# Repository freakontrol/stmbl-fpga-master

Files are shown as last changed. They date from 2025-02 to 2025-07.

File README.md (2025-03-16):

DISCLAIMER
===

THE AUTHORS OF THIS SOFTWARE ACCEPT ABSOLUTELY NO LIABILITY FOR
ANY HARM OR LOSS RESULTING FROM ITS USE.  IT IS _EXTREMELY_ UNWISE
TO RELY ON SOFTWARE ALONE FOR SAFETY.  Any machinery capable of
harming persons must have provisions for completely removing power
from all motors, etc, before persons enter any danger area.  All
machinery must be designed to comply with local and national safety
codes, and the authors of this software can not, and do not, take
any responsibility for such compliance.

This firmware in the folder hostmot2-firmware originates from Mesa Electronics.
This repository  is released under the GPLv3.

STMBL FPGA Master
=====

This is a FPGA controller board specifically designed to be used as a master for up to 12 stmbl drives. It can be used for other applications.
The hardware has the same form factor as the [STMBL](https://github.com/freakontrol/stmbl) v5 drives.
The FPGA runs the hostmot2 firmware.

## Hardware overview
- 12 SSerial ports
- 2 SSerial/RS485 ports
- one 26 Pin parallel expansion port (17 IOs)
- one 24V Input
- one 24V Output
- Host connection via Ethernet or SPI (if used with a RPi 4 or 5)
- 24V Power Input (provides also power to the Raspberry Pi)

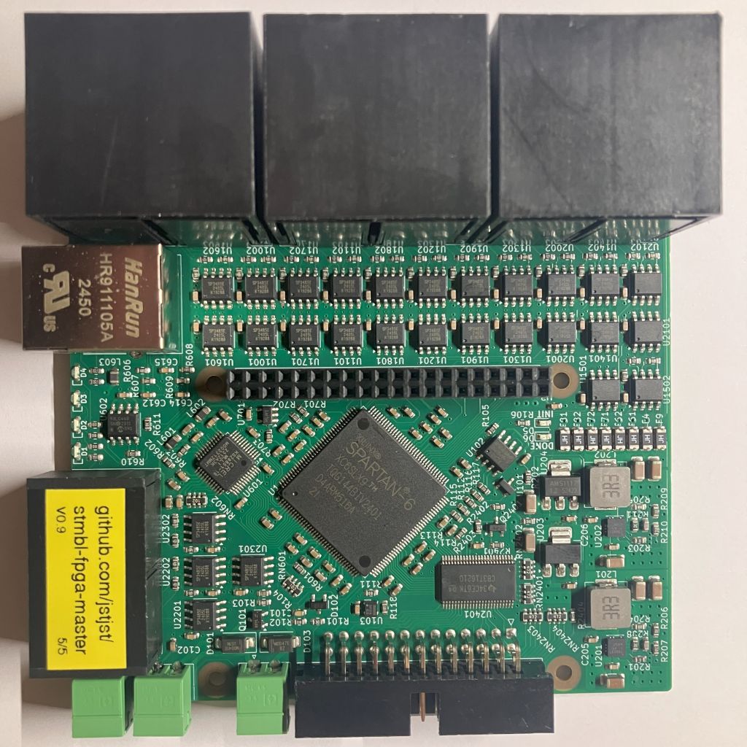
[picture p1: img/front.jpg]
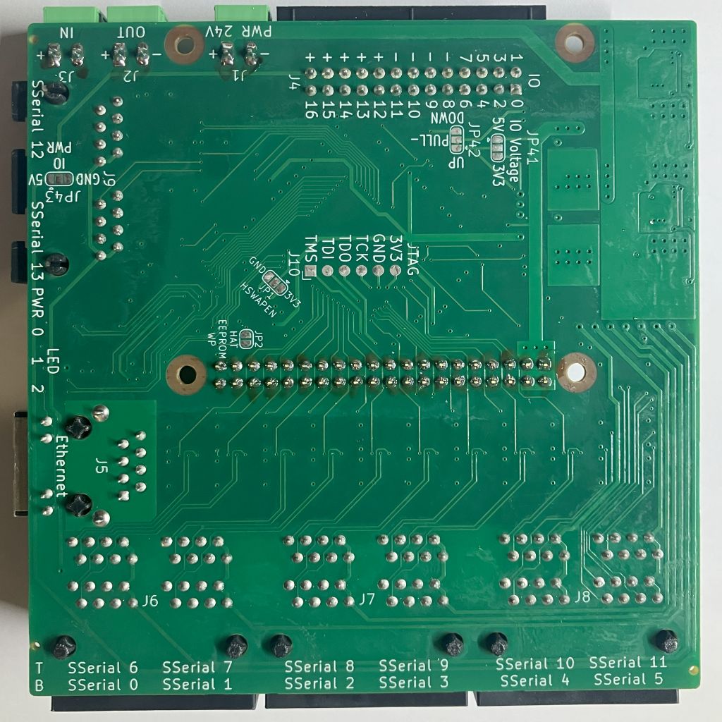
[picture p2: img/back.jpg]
  

## Known Bugs

**Please note that the hardware and firmware are in an early prototyping stage.**
Don't manufacture the version 0.9 because of the reversed SSerial pinouts

- affects hardware v0.9: Pinout of SSerial 0-5 and 12-13 is reversed (1-8, 2-7, ...), use a [Rollover cable](https://en.wikipedia.org/wiki/Rollover_cable)
- SSerial 13 ist not working, there seems to be a bug in the PIN file
- At the moment there is no option to enable power to the SSerial ports before loading the hm2 driver. So it is not possible to use SSerial devices that a powered form the SSerial connector. Can be fixed in firmware.

* * * 
If you have questions about this project contact me [here](https://matrix.to/#/@jst:freiburg.social).

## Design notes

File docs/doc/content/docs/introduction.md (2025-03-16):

---
title: "Introduction"
weight: 1
# bookFlatSection: true
bookToc: true
# bookHidden: false
# bookCollapseSection: true
# bookComments: true
# bookSearchExclude: false
---

# STMBL FPGA Master Introduction Guide

## Description

This is a FPGA controller board specifically designed to be used as a master for up to 12 stmbl drives. It can be used for other applications.
The hardware has the same form factor as the [STMBL](https://github.com/freakontrol/stmbl) v5 drives.
The FPGA runs the hostmot2 firmware.

## Anatomy of the STMBL FPGA Master

The STMBL FPGA Master uses a Spartan 6 and can be either connected via ethernet or SPI to a LinuxCNC host. The board is designed to carry a Raspberry Pi 4 or 5 with the SPI host interface connections.
The board also supplies power to the Raspberry Pi.

{{% hint danger %}}
 Don't connect a USB C power supply to the Raspberry Pi.
{{% /hint %}}

It is also possible to use the board without a Raspberry Pi and connect a host via ethernet.

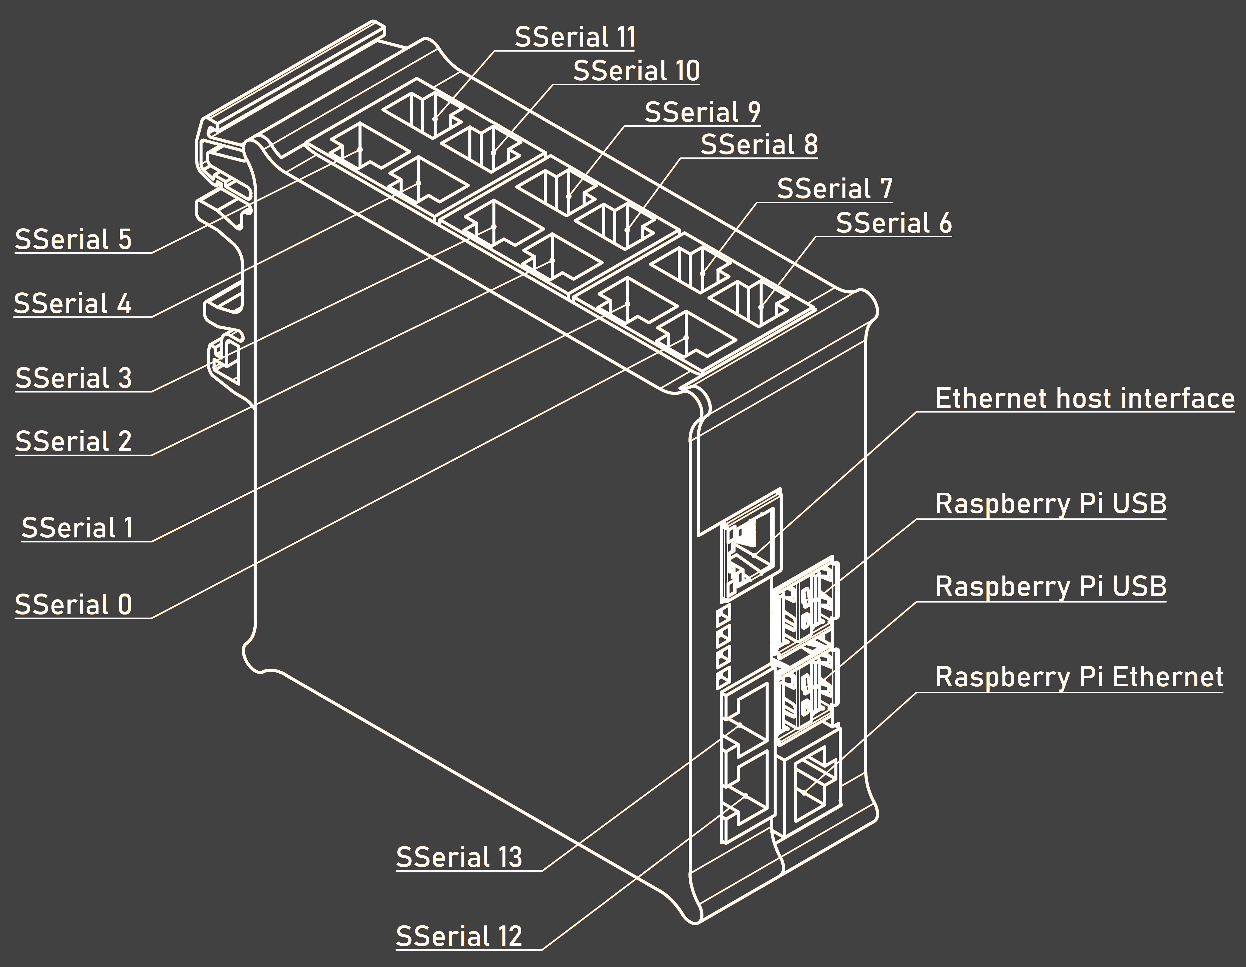
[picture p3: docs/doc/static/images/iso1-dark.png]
STMBL FPGA Master Anatomy


{{% hint danger %}}
 In Hardware v0.9, the Pinout of SSerial 0-5 and 12-13 is reversed (1-8, 2-7, ...), use a [Rollover cable](https://en.wikipedia.org/wiki/Rollover_cable).
{{% /hint %}}

Power to the board should be 24V. A green LED will light when power is supplied.
The board could draw up to 80W if it supplies the SSerial daughter boards and the Raspberry Pi (and USB devices).
For standalone usage the board draws about 2-3W.

{{% hint warning %}}
 A high power consumption is not tested yet, the DC-DC converters might need additional cooling.
{{% /hint %}}

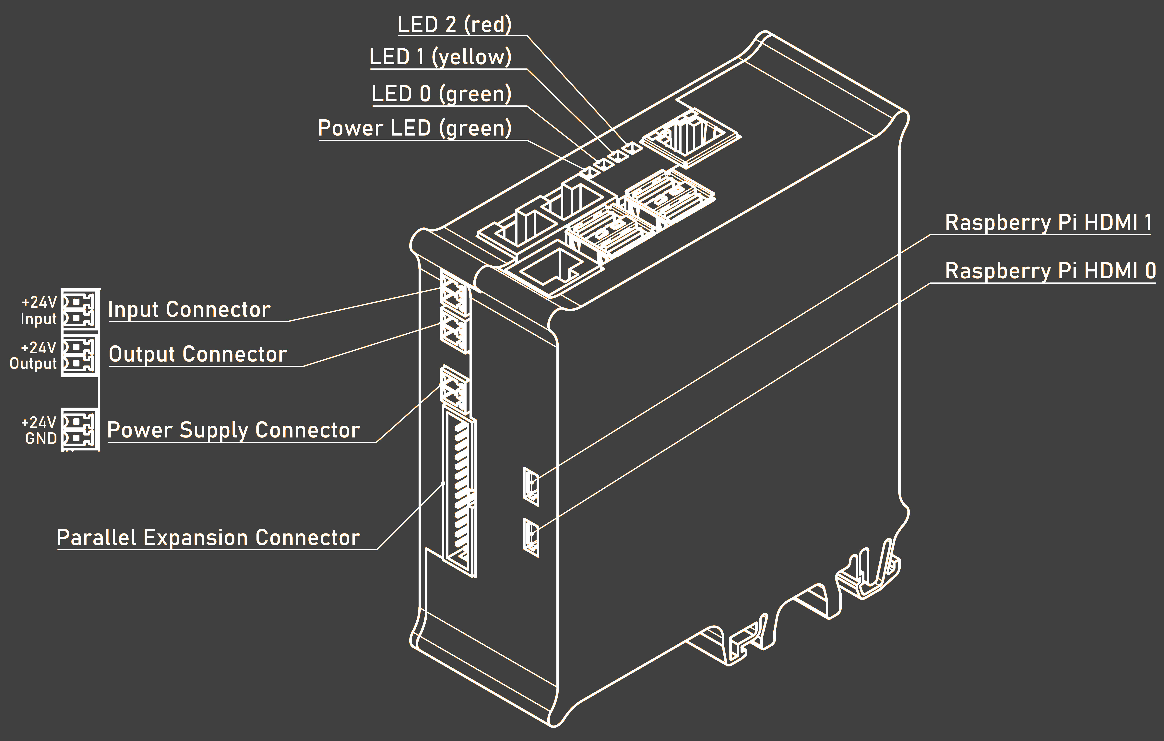
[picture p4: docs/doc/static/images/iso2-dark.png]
STMBL FPGA Master Connectors


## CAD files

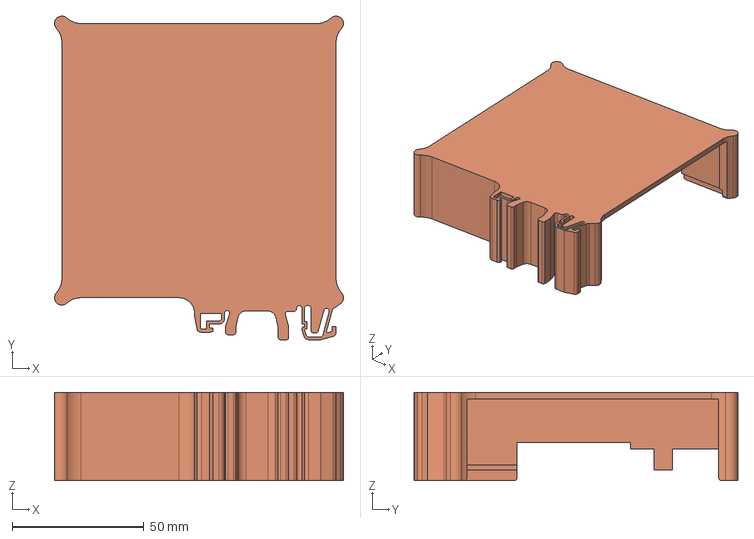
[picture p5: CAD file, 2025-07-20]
3dmodels/stmblv5_ss-kitcase.step
109.6 x 122.8 x 33.5 mm

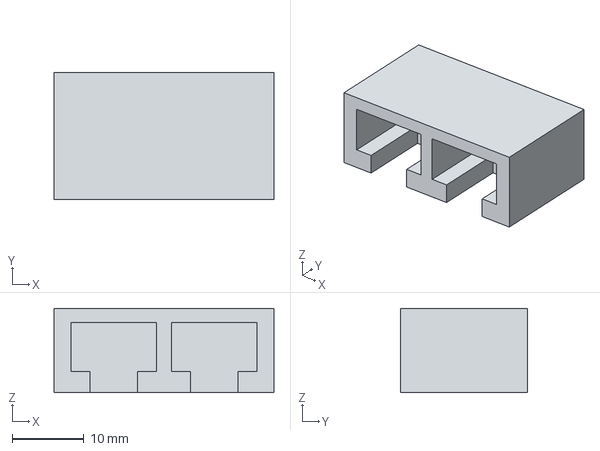
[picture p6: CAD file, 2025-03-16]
3dmodels/HC-RJ45-5622-2-6.step
30.6 x 17.7 x 11.8 mm

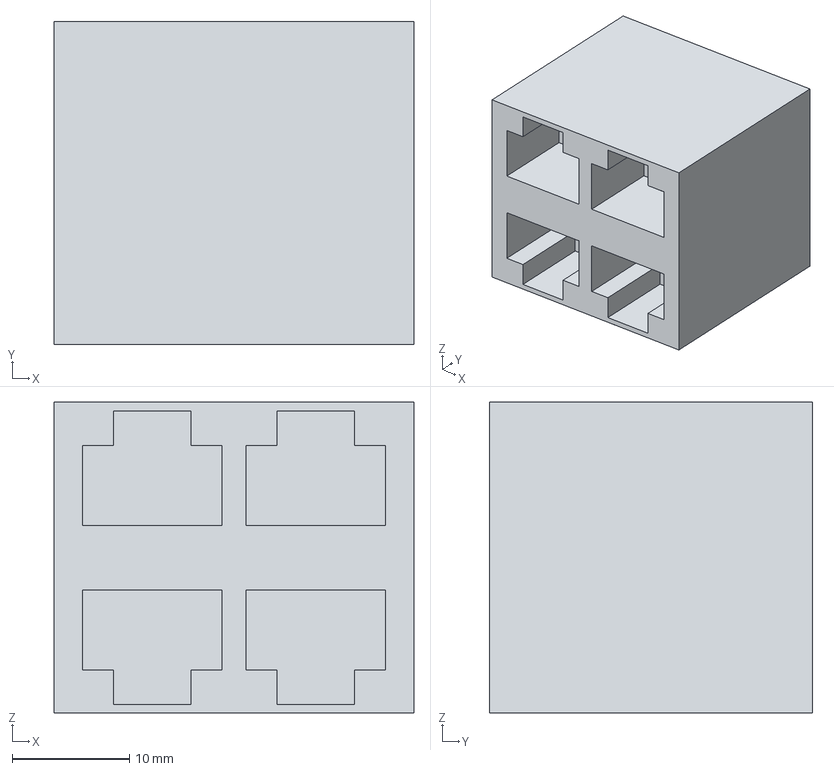
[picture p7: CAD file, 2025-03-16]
3dmodels/MJ5988-B022-HPRN1.step
30.7 x 27.6 x 26.5 mm

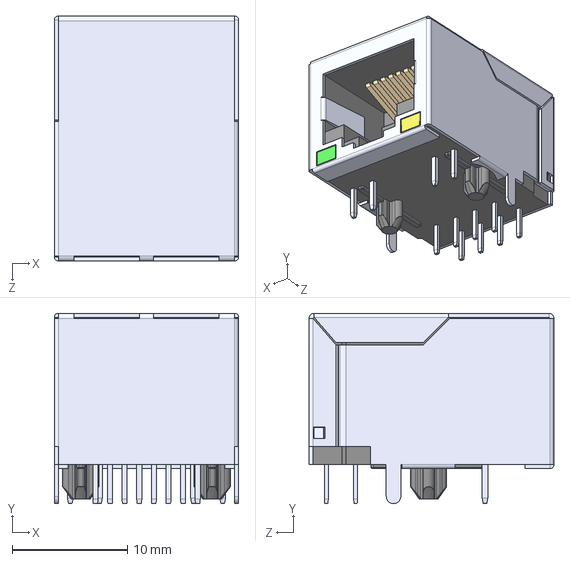
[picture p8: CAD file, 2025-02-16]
3dmodels/HR911105A--3DModel-STEP-56544.STEP
16.0 x 16.6 x 21.3 mm

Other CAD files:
3dmodels/HC-RJ45-5622-2-6.FCStd
3dmodels/MJ5988-B022-HPRN1.FCStd

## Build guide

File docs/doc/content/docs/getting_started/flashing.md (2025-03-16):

---
title: "Flashing"
weight: 2
# bookFlatSection: true
# bookToc: true
# bookHidden: false
# bookCollapseSection: true
# bookComments: true
# bookSearchExclude: false
---

# Flashing a new board

The following guide describes the necessary step to flash a new board.
If your board already has a firmware on it, you can use [mesaflash](https://github.com/jstjst/mesaflash/tree/stmbl-fpga-master).

## Program the FPGA over JTAG

Connect a Raspberry Pi Pico with the [JTAGprobe](https://github.com/dst202/JTAGprobe) firmware to the JTAG port.
Apply 24V to the PWR connector (preferable with a current limited supply).
The green power LED should light up and after a short blink the red INIT and DONE LEDs light up. The board will draw about 60 mA in this state.
You can also hold the JTAG connections on the pads after powering up the board.
Use [OpenOCD](https://openocd.org/) to read out the FPGA device signature:
`openocd -f interface/cmsis-dap.cfg -c "adapter speed 10000; transport select jtag" -f cpld/xilinx-xc6s.cfg -c "init; exit"`

```
Open On-Chip Debugger 0.12.0
Licensed under GNU GPL v2
For bug reports, read
        http://openocd.org/doc/doxygen/bugs.html
jtag
xc6s_print_dna
Info : Using CMSIS-DAPv2 interface with VID:PID=0x2e8a:0x000c, serial=E663AC91D342A338
Info : CMSIS-DAP: SWD supported
Info : CMSIS-DAP: JTAG supported
Info : CMSIS-DAP: Atomic commands supported
Info : CMSIS-DAP: Test domain timer supported
Info : CMSIS-DAP: FW Version = 2.0.0
Info : CMSIS-DAP: Interface Initialised (JTAG)
Info : SWCLK/TCK = 0 SWDIO/TMS = 0 TDI = 0 TDO = 0 nTRST = 0 nRESET = 0
Info : CMSIS-DAP: Interface ready
Info : clock speed 10000 kHz
Info : cmsis-dap JTAG TLR_RESET
Info : cmsis-dap JTAG TLR_RESET
Info : JTAG tap: xc6s.tap tap/device found: 0x24001093 (mfg: 0x049 (Xilinx), part: 0x4001, ver: 0x2)
Warn : gdb services need one or more targets defined
```

If you get the device signatur above, you can flash the board:
`openocd -f interface/cmsis-dap.cfg -c "adapter speed 10000; transport select jtag" -f cpld/xilinx-xc6s.cfg -c "init; xc6s_program xc6s.tap; pld load 0 hostmot2-firmware/bit/stmblETH_FALLBACK.bit; exit"`

```
Open On-Chip Debugger 0.12.0
Licensed under GNU GPL v2
For bug reports, read
        http://openocd.org/doc/doxygen/bugs.html
jtag
xc6s_print_dna
Info : Using CMSIS-DAPv2 interface with VID:PID=0x2e8a:0x000c, serial=E663AC91D342A338
Info : CMSIS-DAP: SWD supported
Info : CMSIS-DAP: JTAG supported
Info : CMSIS-DAP: Atomic commands supported
Info : CMSIS-DAP: Test domain timer supported
Info : CMSIS-DAP: FW Version = 2.0.0
Info : CMSIS-DAP: Interface Initialised (JTAG)
Info : SWCLK/TCK = 0 SWDIO/TMS = 0 TDI = 0 TDO = 0 nTRST = 0 nRESET = 0
Info : CMSIS-DAP: Interface ready
Info : clock speed 10000 kHz
Info : cmsis-dap JTAG TLR_RESET
Info : cmsis-dap JTAG TLR_RESET
Info : JTAG tap: xc6s.tap tap/device found: 0x24001093 (mfg: 0x049 (Xilinx), part: 0x4001, ver: 0x2)
Warn : gdb services need one or more targets defined
Info : cmsis-dap JTAG TLR_RESET
```

The programming takes about one minute, after programming openocd will exit.
If the programming was sucsessfull the INIT LED should blink (indicating that a fallback bit file was flashed), continue with [Write the ethernet EEPROM](flashing/#write-the-ethernet-eeprom) without powering down the board.
If you have trouble with the programming, try to solder the JTAG connector (there is no verification of the program).

## Write the ethernet EEPROM

Connect to the board via Ethernet.
{{% hint danger %}}
 Only the `J5` RJ45 connector is a ethernet port, the other RJ45 connectors are SSerial ports and may damage your PC.
{{% /hint %}}

Set your network config appropriately and try to ping the board `ping -c 4 192.168.1.121`

```
PING 192.168.1.121 (192.168.1.121) 56(84) bytes of data.
64 bytes from 192.168.1.121: icmp_seq=1 ttl=63 time=0.622 ms
64 bytes from 192.168.1.121: icmp_seq=2 ttl=63 time=0.636 ms
64 bytes from 192.168.1.121: icmp_seq=3 ttl=63 time=1.10 ms
64 bytes from 192.168.1.121: icmp_seq=4 ttl=63 time=1.49 ms

--- 192.168.1.121 ping statistics ---
4 packets transmitted, 4 received, 0% packet loss, time 3055ms
rtt min/avg/max/mdev = 0.622/0.961/1.488/0.359 ms
```

Use the script `tools/init/stmblETH-init.sh` to write the board name and mac address to the EEPROM.

```
Old Name: ����������������
New Name: stmblETH

Old MAC Addr: 00FFFFFFFFFF
New MAC Addr: 0073746D626C

Reseting Ethernet CPU
```

{{% hint warning %}}
 If you use more than one board, you should set different MAC addresses.
{{% /hint %}}

After writing the values to the EEPROM continue with [Write the bit file in the SPI flash](flashing/#write-the-bit-file-in-the-spi-flash) without powering down the board.

## Write the bit file in the SPI flash

Check if mesaflash recognizes the board: `./mesaflash --device ether --addr 192.168.1.121`

```
ETH device stmblETH at ip=192.168.1.121
```

Flash the fallback firmware and boot block: `./mesaflash --device ether --addr 192.168.1.121 --fix-boot-block --fallback --write hostmot2-firmware/bit/stmblETH_FALLBACK.bit`

```
Checking file... OK
  File type: Xilinx bit file
Boot sector OK
FLASH memory sectors to write: 6, max sectors in area: 15
Erasing FLASH memory sectors starting from 0x10000...
  |EEEEEE
Programming FLASH memory sectors starting from 0x10000...
  |WWWWWWWWWWWWWWWWWWWWWWWWWWWWWWWWWWWWWWWWWW
Board configuration updated successfully.
Checking file... OK
  File type: Xilinx bit file
Boot sector OK
Verifying FLASH memory sectors starting from 0x10000...
  |VVVVVVVVVVVVVVVVVVVVVVVVVVVVVVVVVVVVVVVVVV
Board configuration verified successfully.

You must power cycle the hardware or use the --reload command to load a new firmware.
```

Flash the main firmware: `./mesaflash --device ether --addr 192.168.1.121 --write hostmot2-firmware/bit/stmblETH_SSD13.bit`

```
Checking file... OK
  File type: Xilinx bit file
Boot sector OK
FLASH memory sectors to write: 6, max sectors in area: 16
Erasing FLASH memory sectors starting from 0x100000...
  |EEEEEE
Programming FLASH memory sectors starting from 0x100000...
  |WWWWWWWWWWWWWWWWWWWWWWWWWWWWWWWWWWWWWWWWWW
Board configuration updated successfully.
Checking file... OK
  File type: Xilinx bit file
Boot sector OK
Verifying FLASH memory sectors starting from 0x100000...
  |VVVVVVVVVVVVVVVVVVVVVVVVVVVVVVVVVVVVVVVVVV
Board configuration verified successfully.

You must power cycle the hardware or use the --reload command to load a new firmware.
```

You can also flash a firmware for usage with the SPI host interface, but you will lose ethernet connectivity afterwards.

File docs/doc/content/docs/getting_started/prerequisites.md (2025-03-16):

---
title: "Prerequisites"
weight: 1
# bookFlatSection: false
# bookToc: true
# bookHidden: false
# bookCollapseSection: false
# bookComments: false
# bookSearchExclude: false
---

# Prerequisites

## JTAG programming

If your are programming a new (empty) board, you need a JTAG programmer. I used a Raspberry Pi Pico with the [JTAGprobe](https://github.com/dst202/JTAGprobe) firmware and [OpenOCD](https://openocd.org/).
I also tried to us a FT232RL in combination with openFPGALoader, which for some reason didn't work.

## Host interface

Regardless of whether you use SPI or Ethernet, all the usual requirements for normal mesa cards apply here.
It is recommended to initially flash the board over Ethernet.

## Mesaflash

In order for Mesaflash to recognize the board, you need to compile this adapted version: https://github.com/jstjst/mesaflash/tree/stmbl-fpga-master

## LinuxCNC

In order for LinuxCNC to recognize the board, you need to compile this adapted version: https://github.com/jstjst/linuxcnc/tree/stmbl-fpga-master

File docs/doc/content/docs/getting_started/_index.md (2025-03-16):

---
weight: 2
# bookFlatSection: true
# bookToc: true
# bookHidden: false
bookCollapseSection: true
# bookComments: true
# bookSearchExclude: false
---

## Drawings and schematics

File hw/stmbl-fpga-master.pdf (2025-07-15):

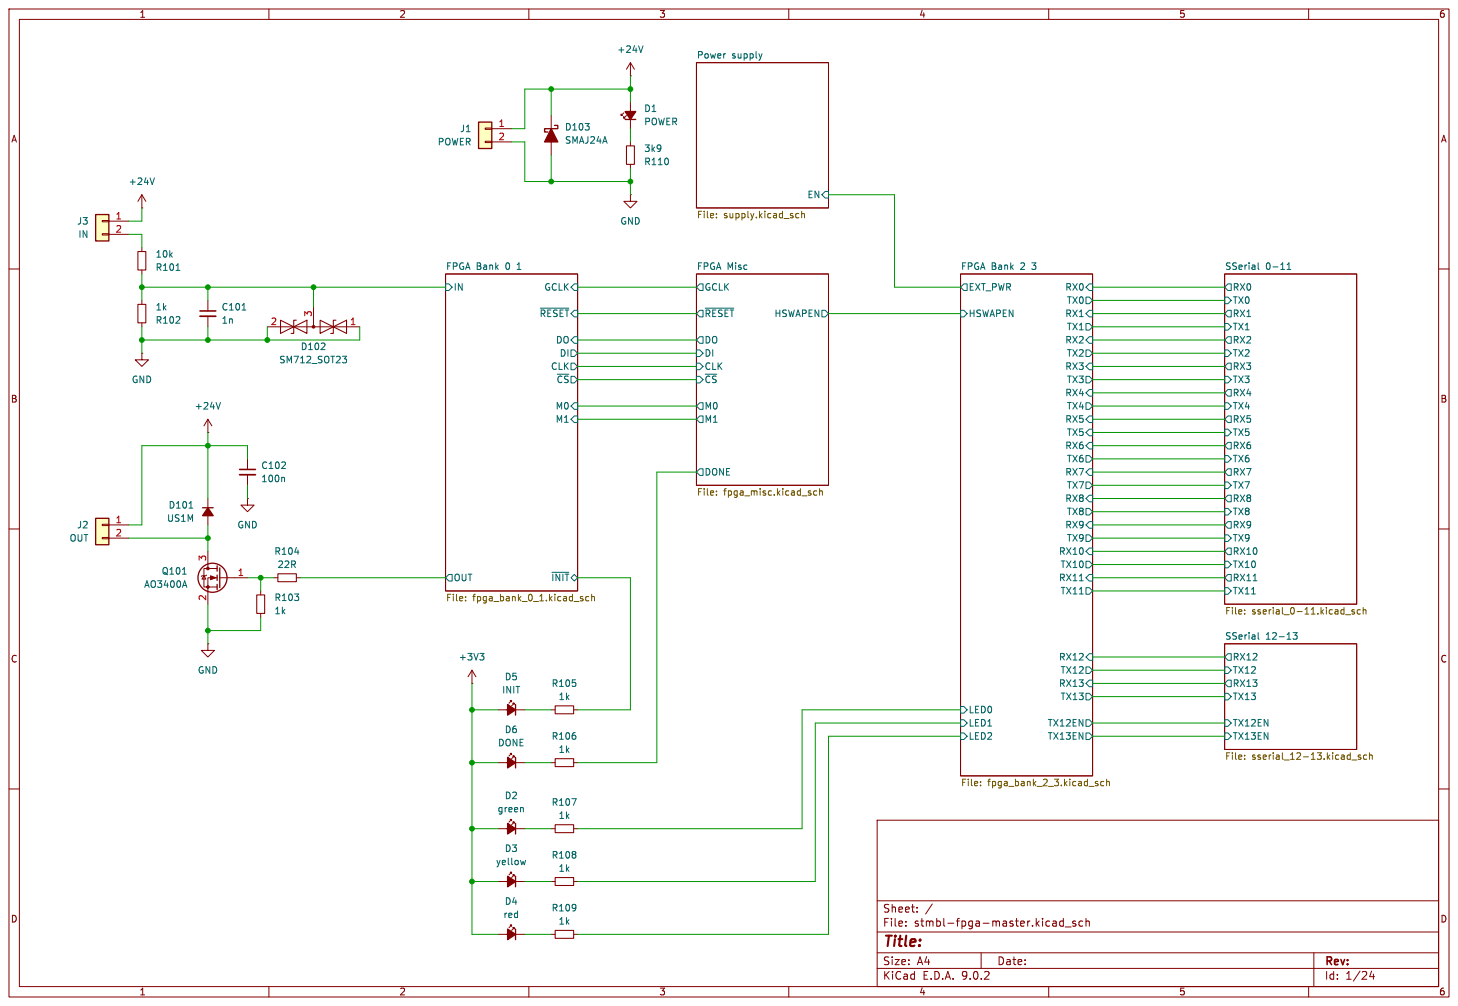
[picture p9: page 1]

Power supply File: supply.kicad_sch

FPGA Bank 2 3 File: fpga_bank_2_3.kicad_sch CLK
~{CS} GCLK M1DI DO
~{RESET} M0 ~{INIT}

~{RESET} GCLK DONE M0 M1 DO

Id: 1/24 Title: File: stmbl-fpga-master.kicad_sch Sheet: /

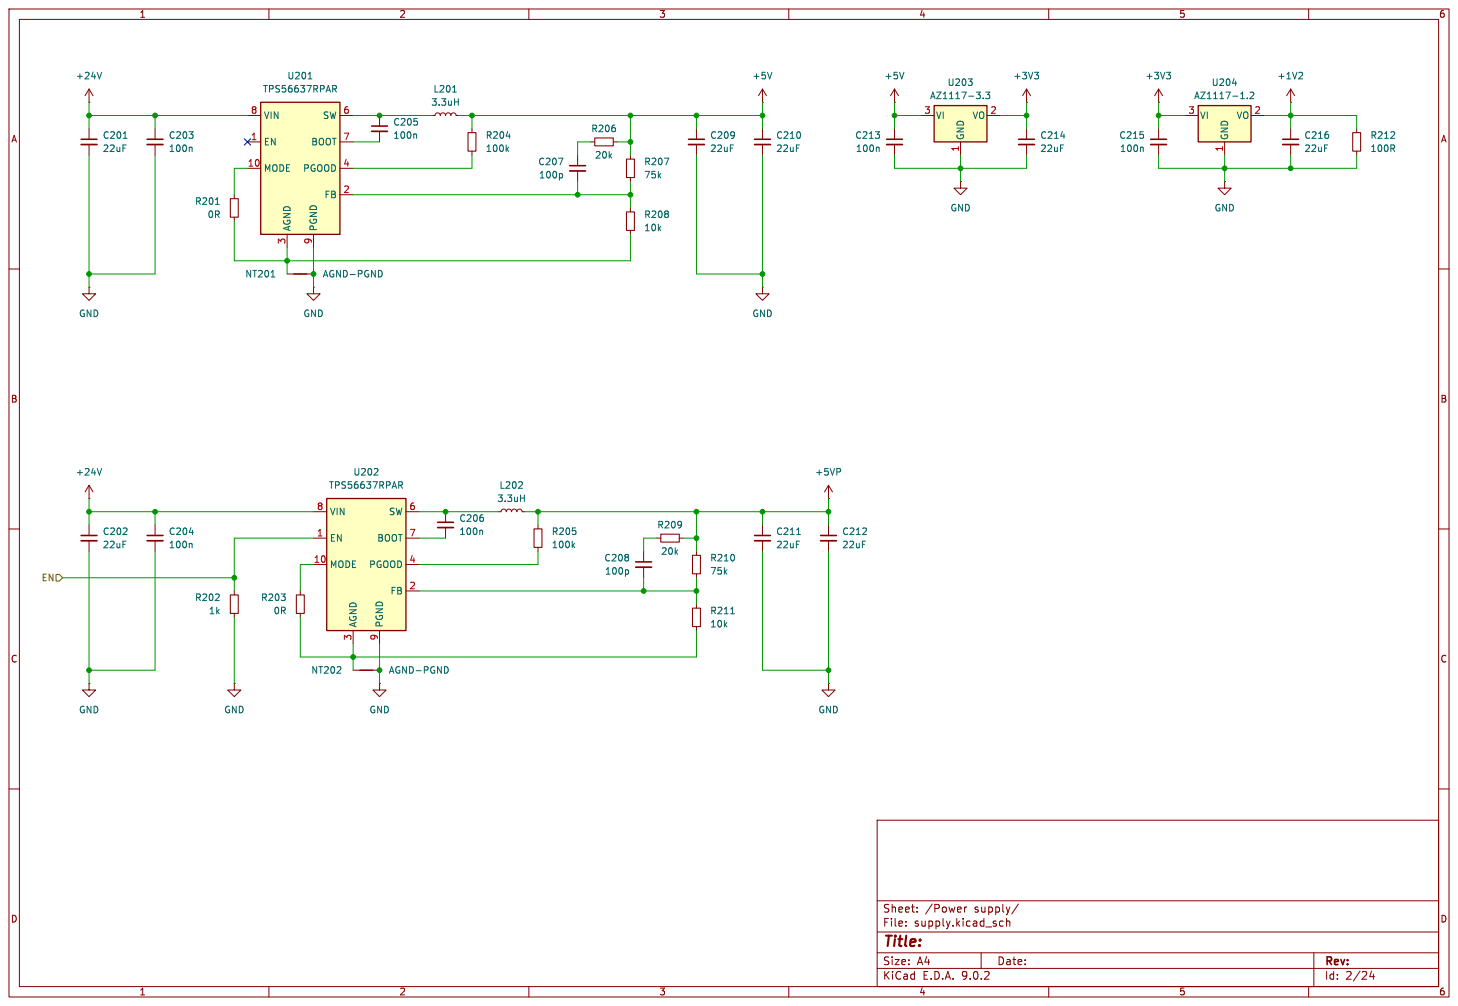
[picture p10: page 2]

9 SW 6 BOOT 7 PGOOD 4 FB 2 U201 TPS56637RPAR GND

1 VO 2 U204 AZ1117-1.2 NT202 AGND-PGND GND

9 SW 6 BOOT 7 PGOOD 4 FB 2 U202 TPS56637RPAR

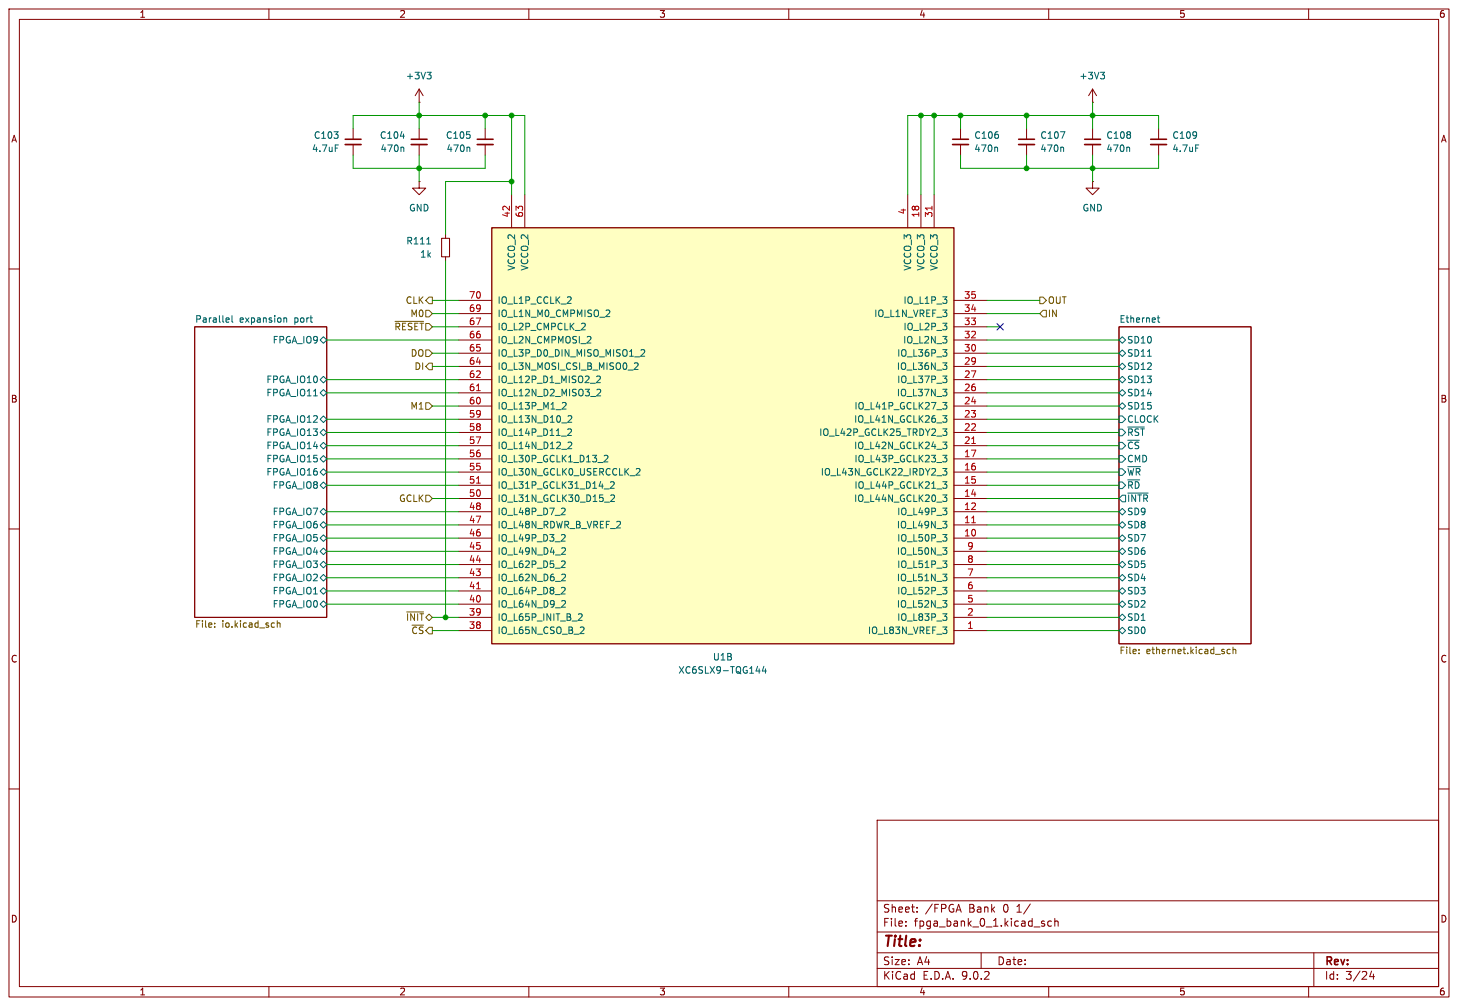
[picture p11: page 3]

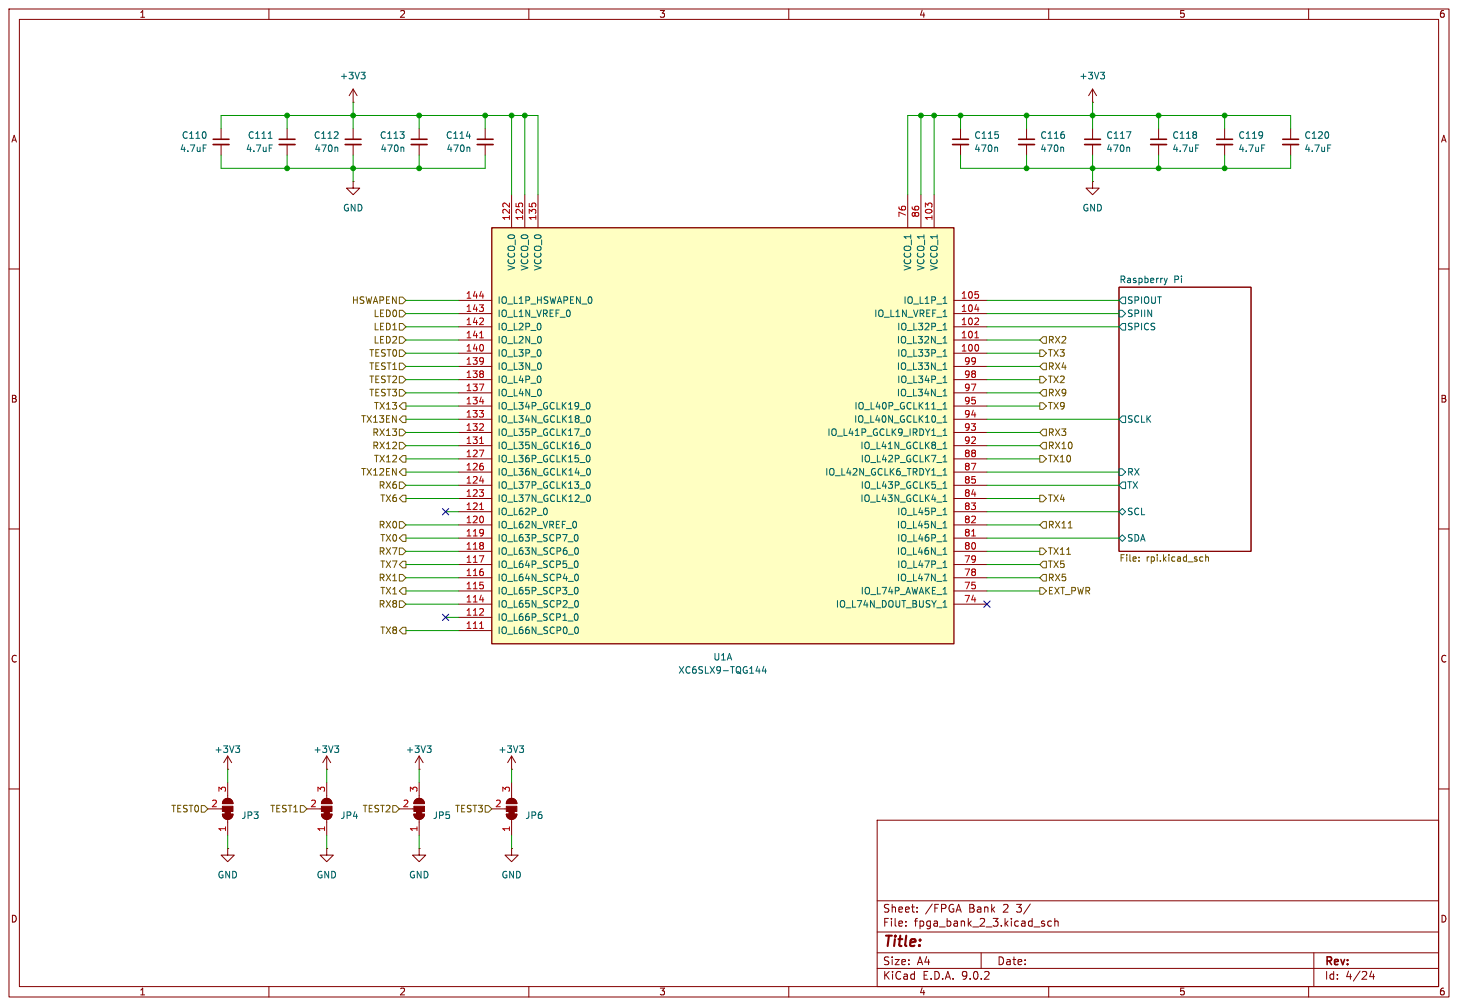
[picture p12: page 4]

TX Raspberry Pi File: rpi.kicad_sch C115

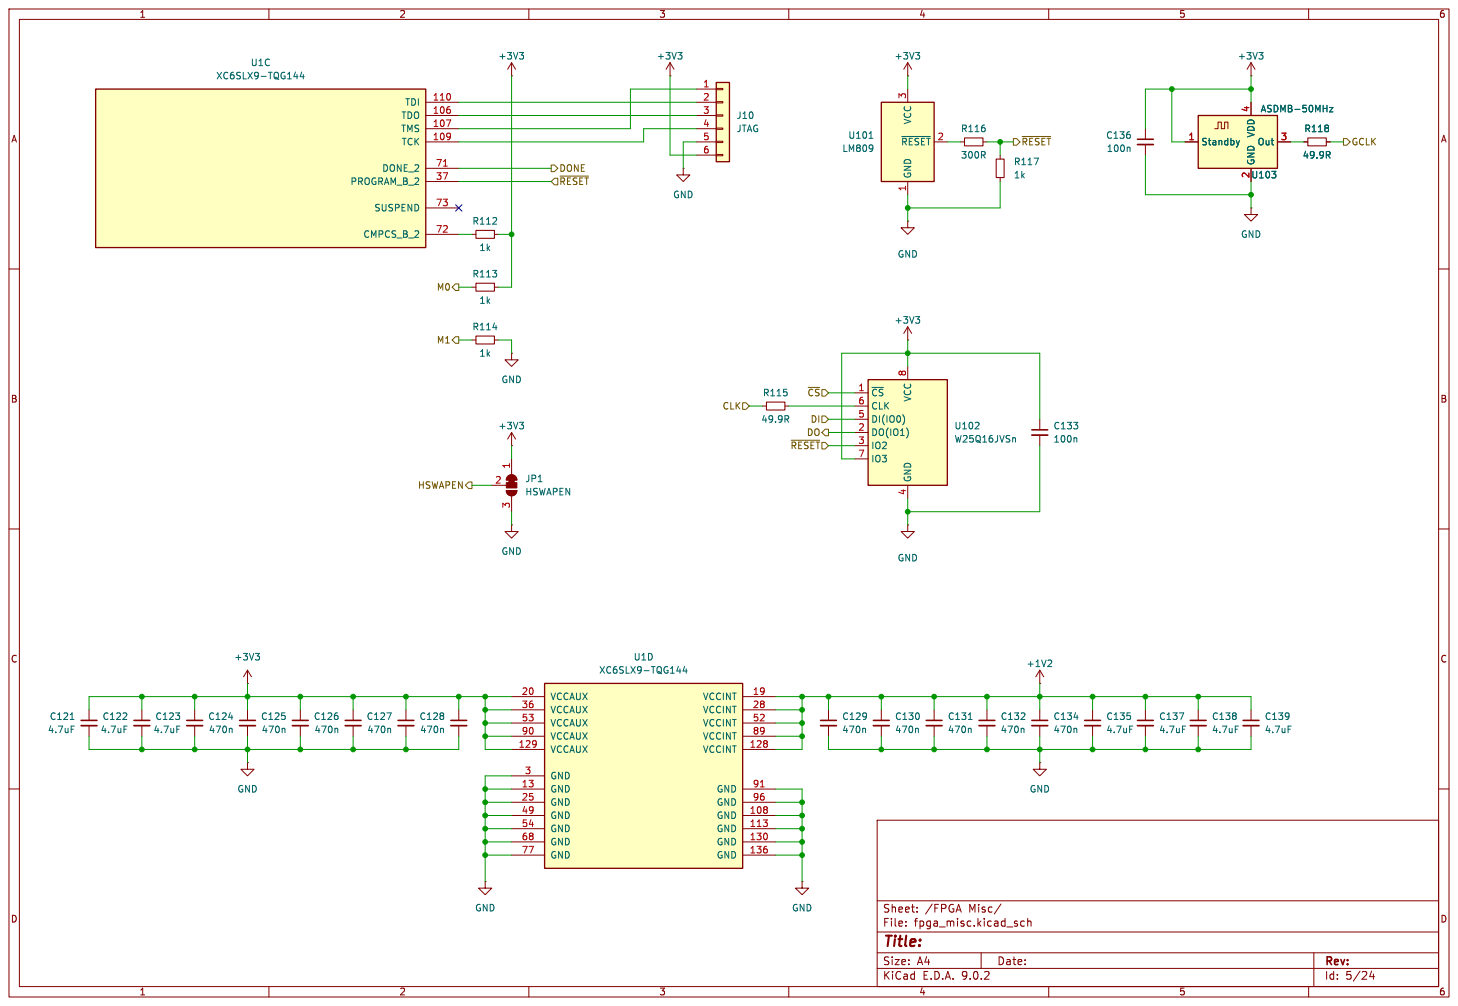
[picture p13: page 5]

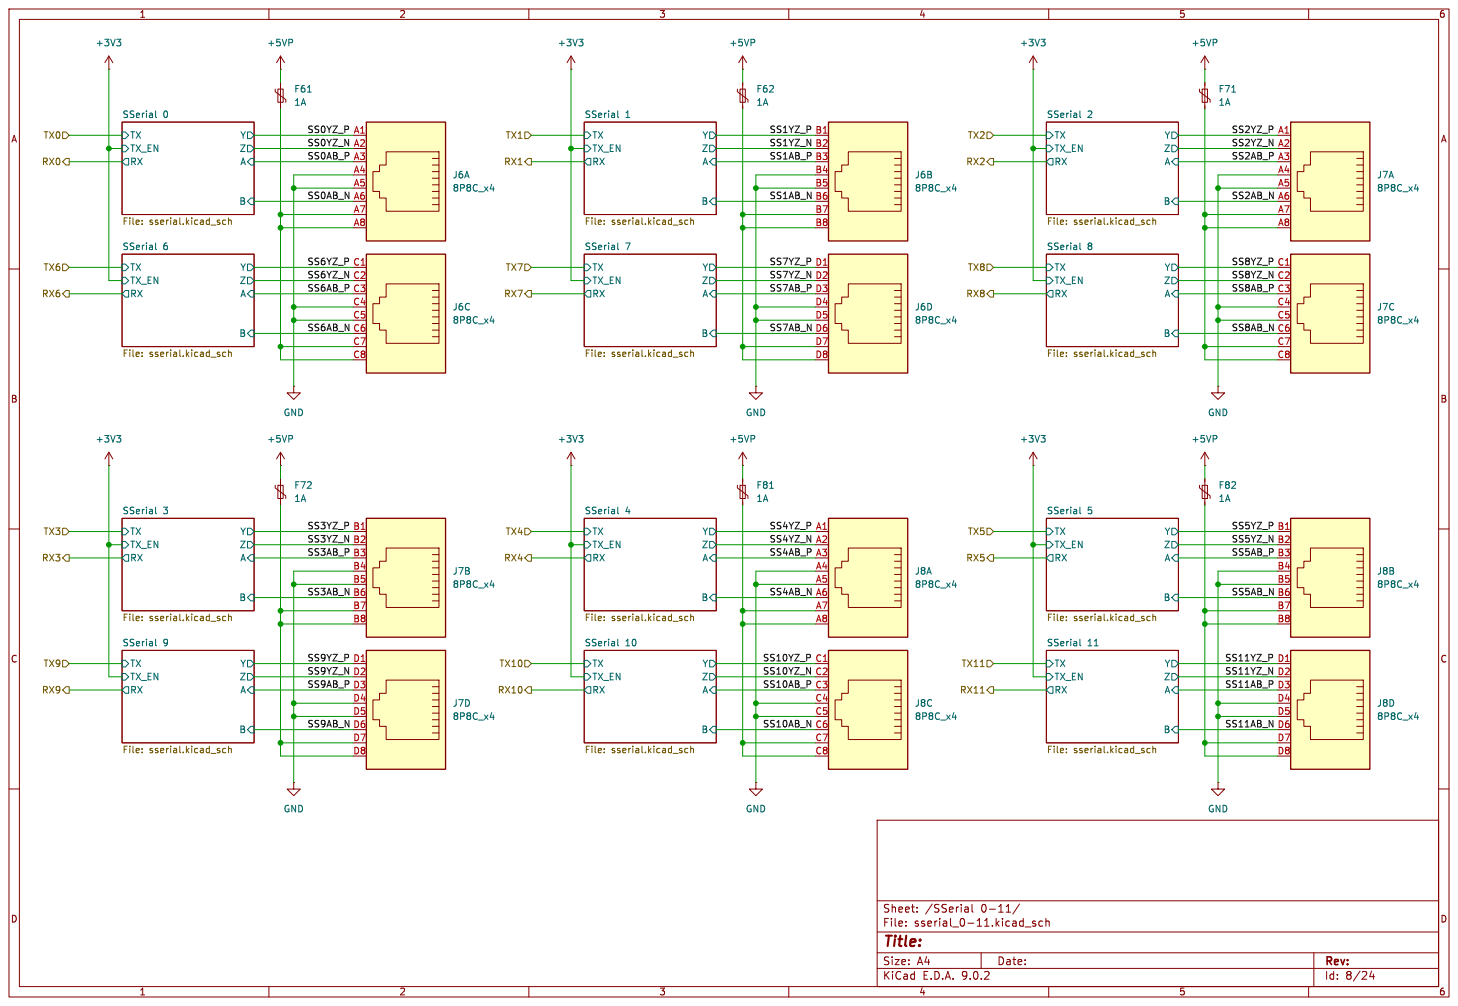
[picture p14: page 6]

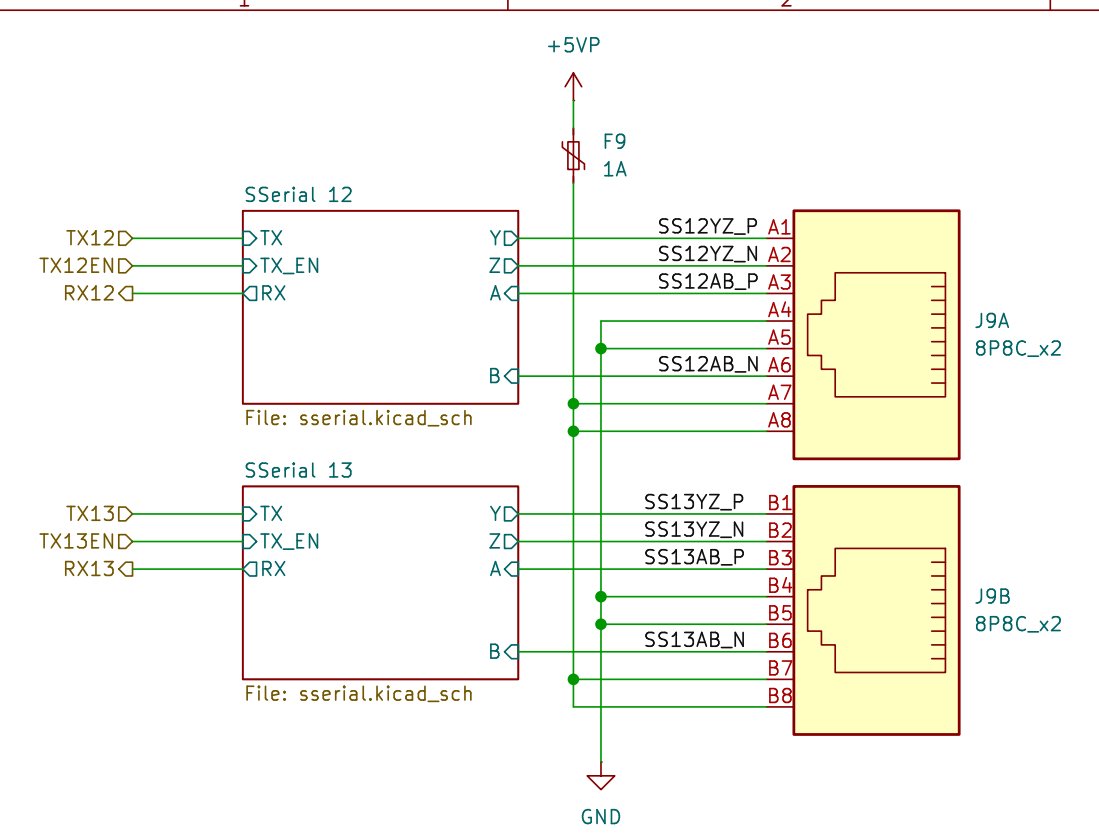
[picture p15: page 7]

SS12YZ_N
SS12AB_P

SS13YZ_N
SS13AB_P

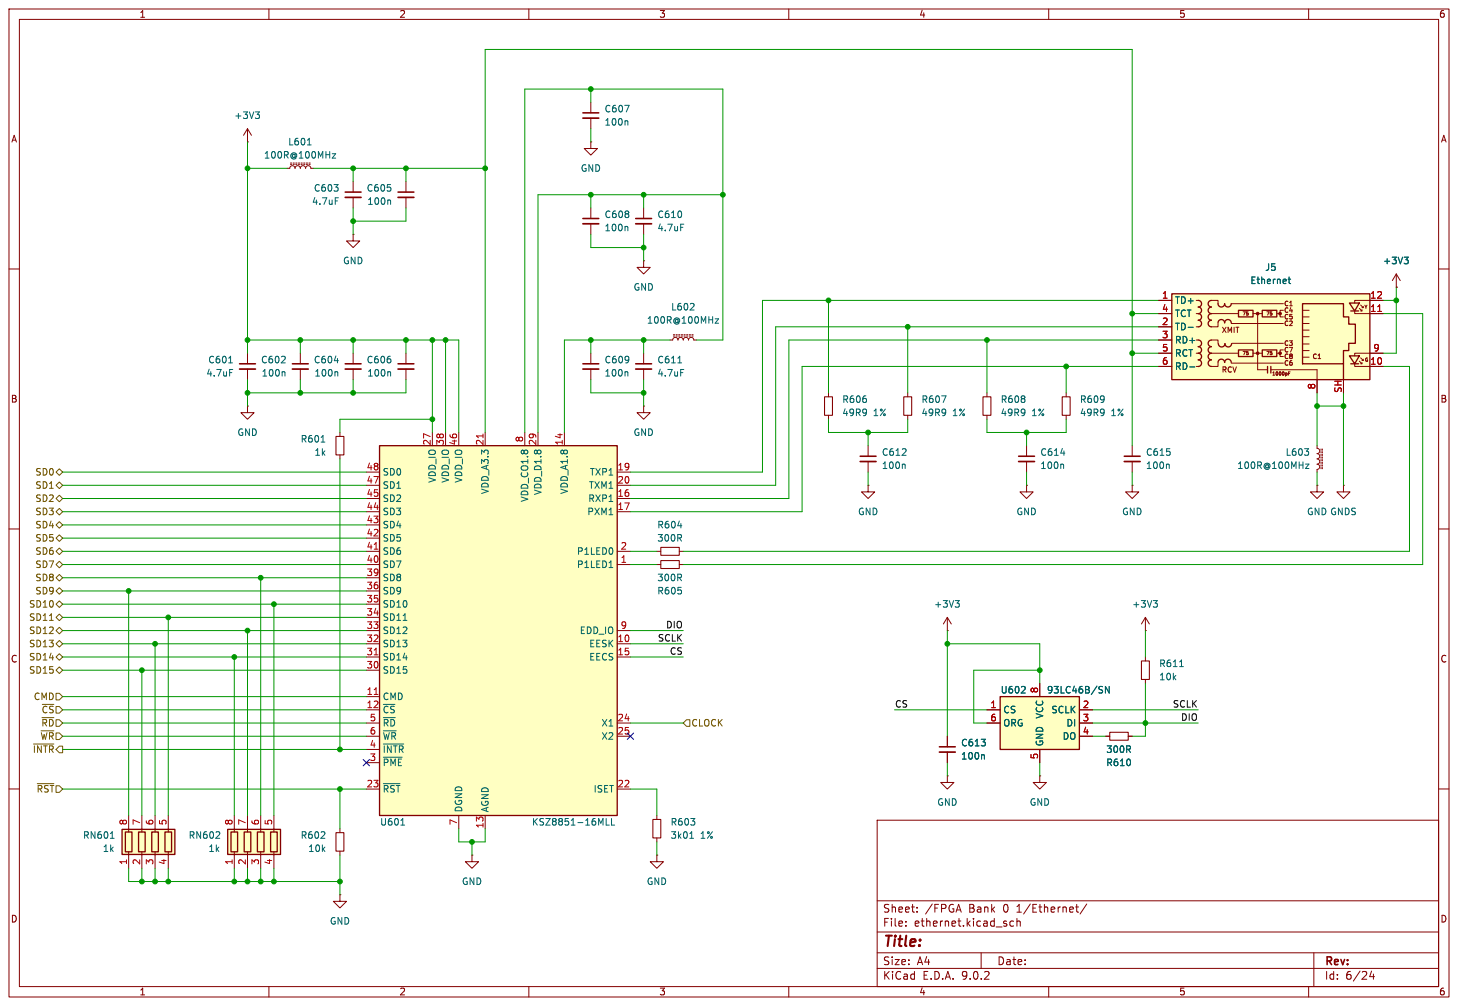
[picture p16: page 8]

J5 Ethernet TD+ 1 TCT 4 TD- 2 RD+ 3 RCT 5 RD- 6

YG TD+ 1 TCT 4 TD- 2 RD+ 3 RCT 5 RD- 6

5 SCLK 2 DI 3 DO 4 U602 93LC46B/SN GND

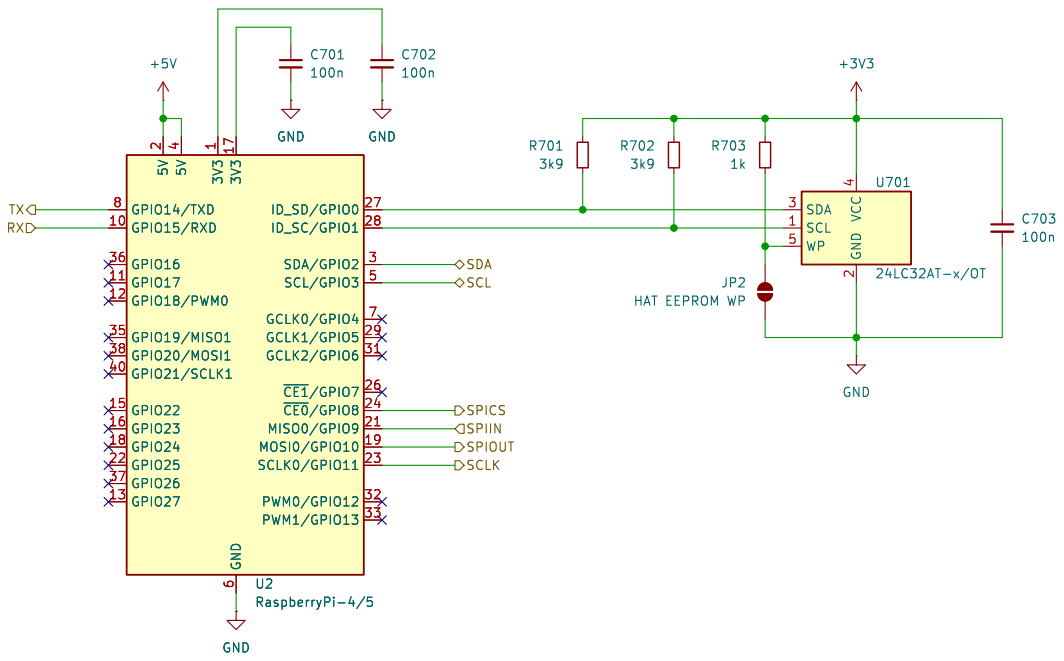
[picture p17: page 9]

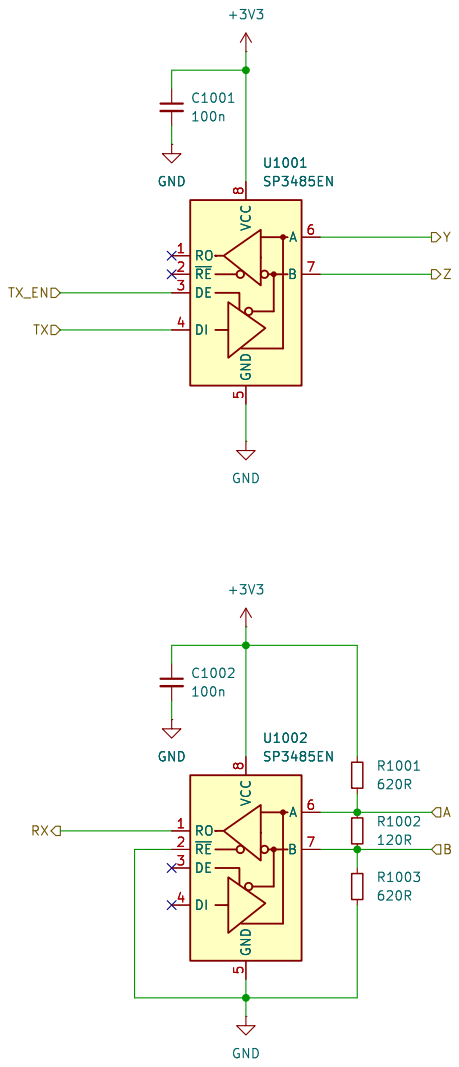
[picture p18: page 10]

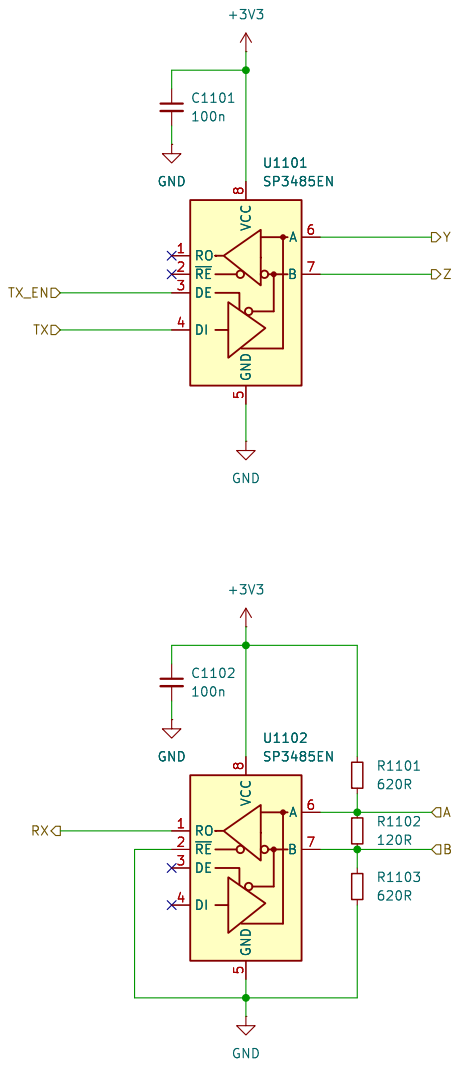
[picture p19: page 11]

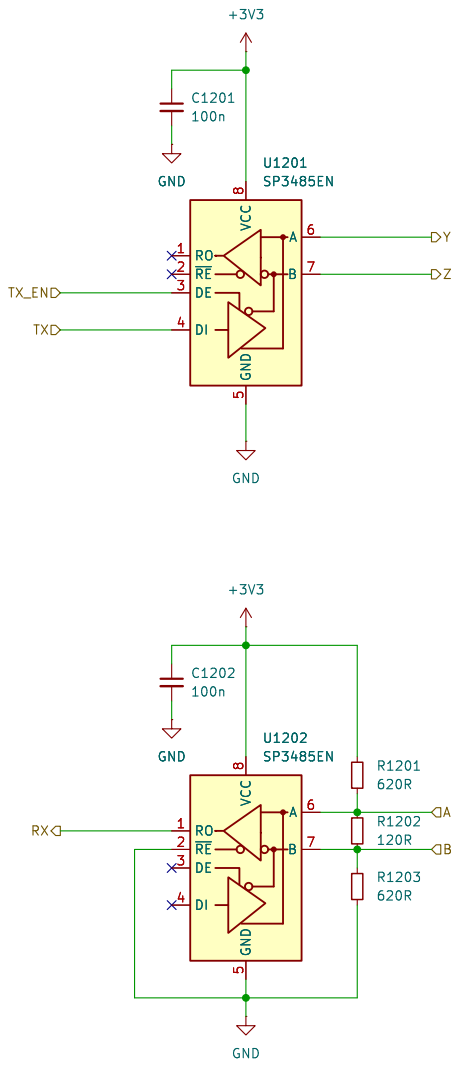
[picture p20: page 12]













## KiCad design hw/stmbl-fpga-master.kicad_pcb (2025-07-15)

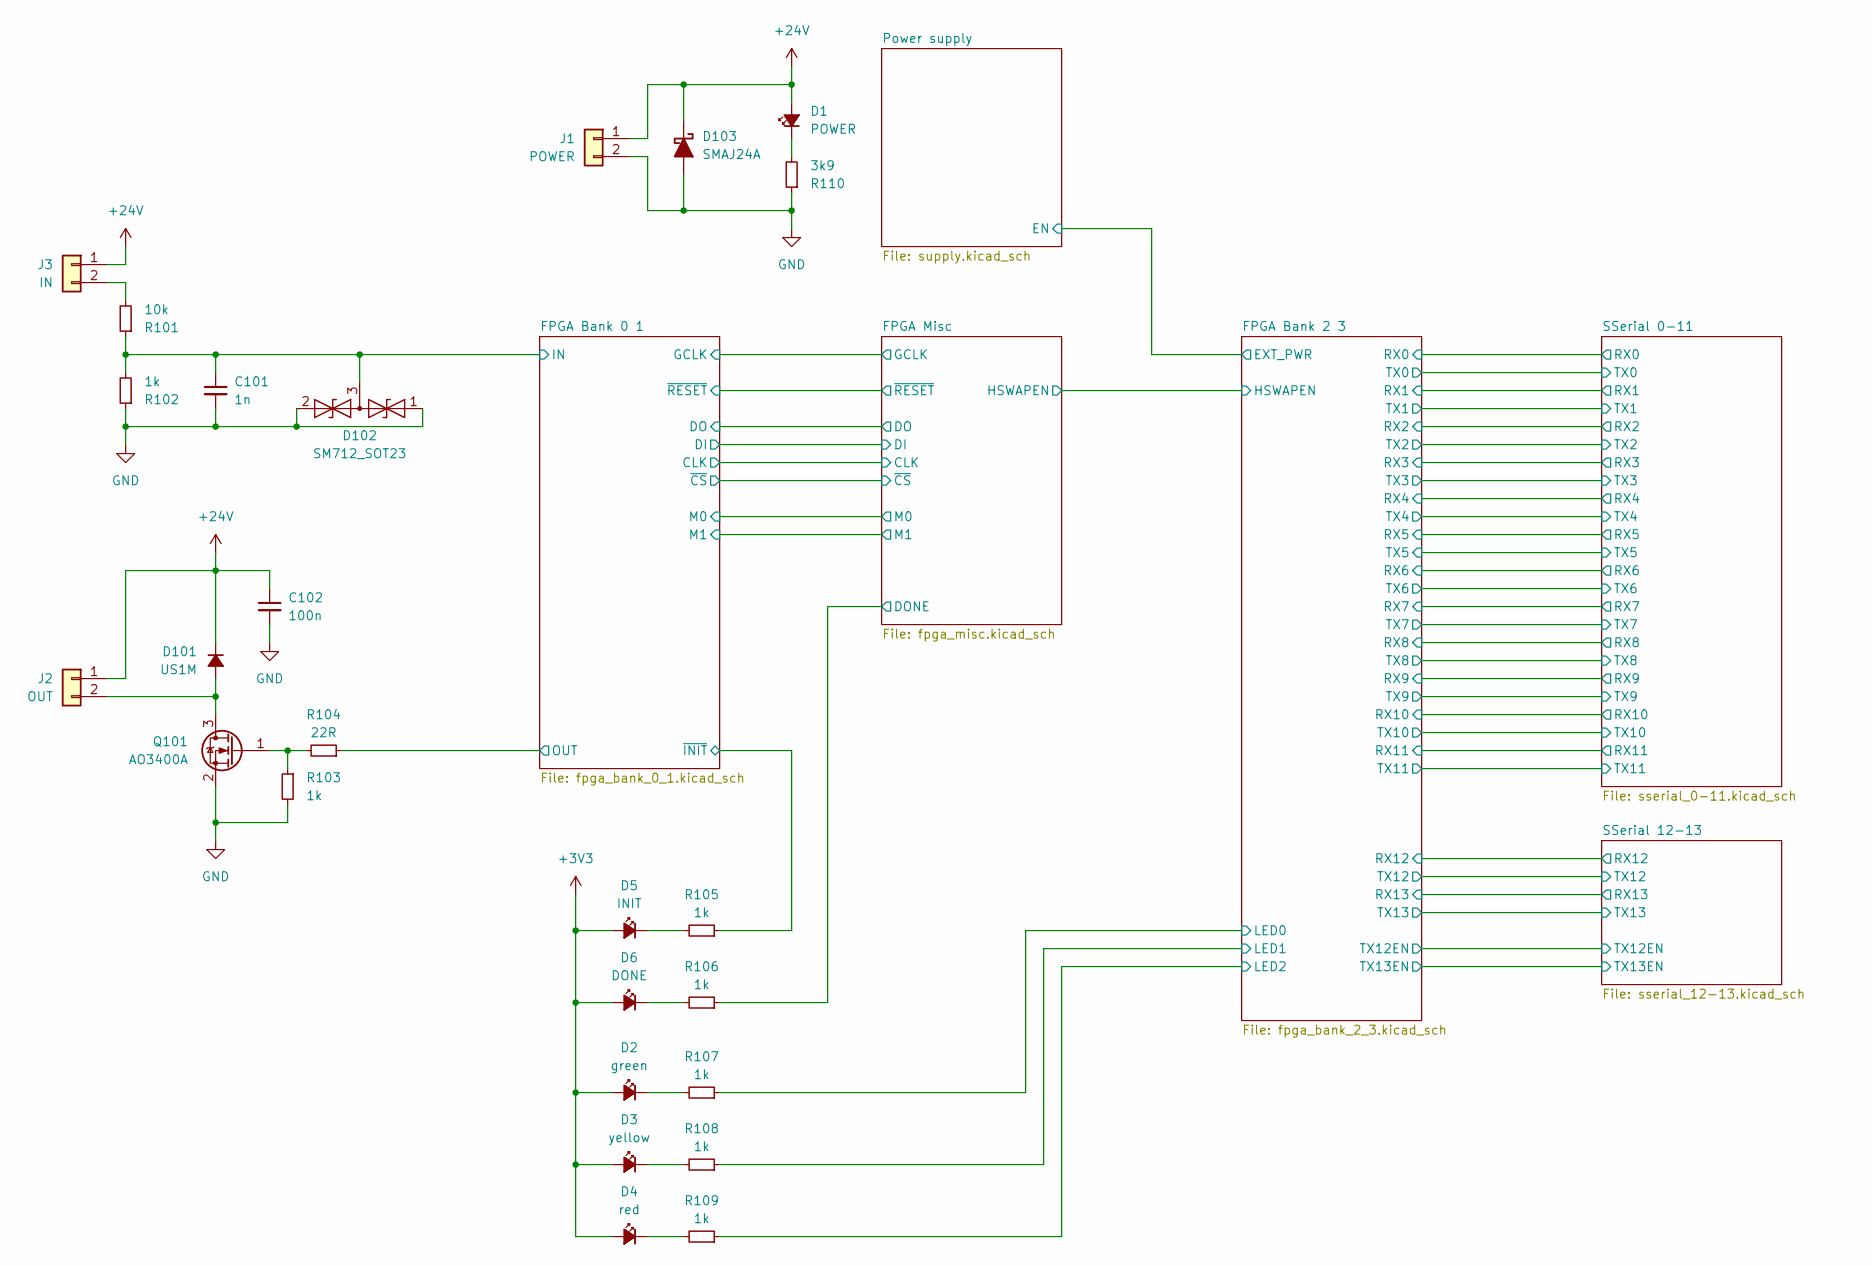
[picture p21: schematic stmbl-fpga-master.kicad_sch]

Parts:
C101: 1n; C_0603_1608Metric
C102: 100n; C_0603_1608Metric
D1: POWER; LED-0805-SIDE
D2: green; LED-0805-SIDE
D3: yellow; LED-0805-SIDE
D4: red; LED-0805-SIDE
D5: INIT; LED_0603_1608Metric
D6: DONE; LED_0603_1608Metric
D101: US1M; D_SMA
D102: SM712_SOT23; SOT-23
D103: SMAJ24A; D_SMA
J1: POWER; PhoenixContact_MC_1,5_2-G-3.5_1x02_P3.50mm_Horizontal
J2: OUT; PhoenixContact_MC_1,5_2-G-3.5_1x02_P3.50mm_Horizontal
J3: IN; PhoenixContact_MC_1,5_2-G-3.5_1x02_P3.50mm_Horizontal
Q101: AO3400A; SOT-23
R101: 10k; R_0603_1608Metric
R102, R103, R105, R106, R107, R108, R109: 1k; R_0603_1608Metric
R104: 22R; R_0603_1608Metric
R110: 3k9; R_0603_1608Metric

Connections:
+3V3: D2.2 (A), D3.2 (A), D4.2 (A), D5.2 (A), D6.2 (A); also elsewhere on the board
+24V: C102.1, D1.2 (A), D101.1 (K), D103.1 (K), J1.1, J2.1, J3.1; also elsewhere on the board
/FPGA Bank 0 1/IN: C101.1, D102.3 (common), R101.1, R102.2; also elsewhere on the board
/FPGA Bank 0 1/OUT: R104.1; also elsewhere on the board
/FPGA Bank 0 1/~INIT: R105.1; also elsewhere on the board
/FPGA Bank 2 3/LED0: R107.1; also elsewhere on the board
/FPGA Bank 2 3/LED1: R108.1; also elsewhere on the board
/FPGA Bank 2 3/LED2: R109.1; also elsewhere on the board
/FPGA Misc/DONE: R106.1; also elsewhere on the board
GND: C101.2, C102.2, D102.1 (A1), D102.2 (A2), D103.2 (A), J1.2, Q101.2 (S), R102.1, R103.2, R110.1; also elsewhere on the board
unnamed: D1.1 (K), R110.2
unnamed: D2.1 (K), R107.2
unnamed: D3.1 (K), R108.2
unnamed: D4.1 (K), R109.2
unnamed: D5.1 (K), R105.2
unnamed: D6.1 (K), R106.2
unnamed: D101.2 (A), J2.2, Q101.3 (D)
unnamed: J3.2, R101.2
unnamed: Q101.1 (G), R103.1, R104.2

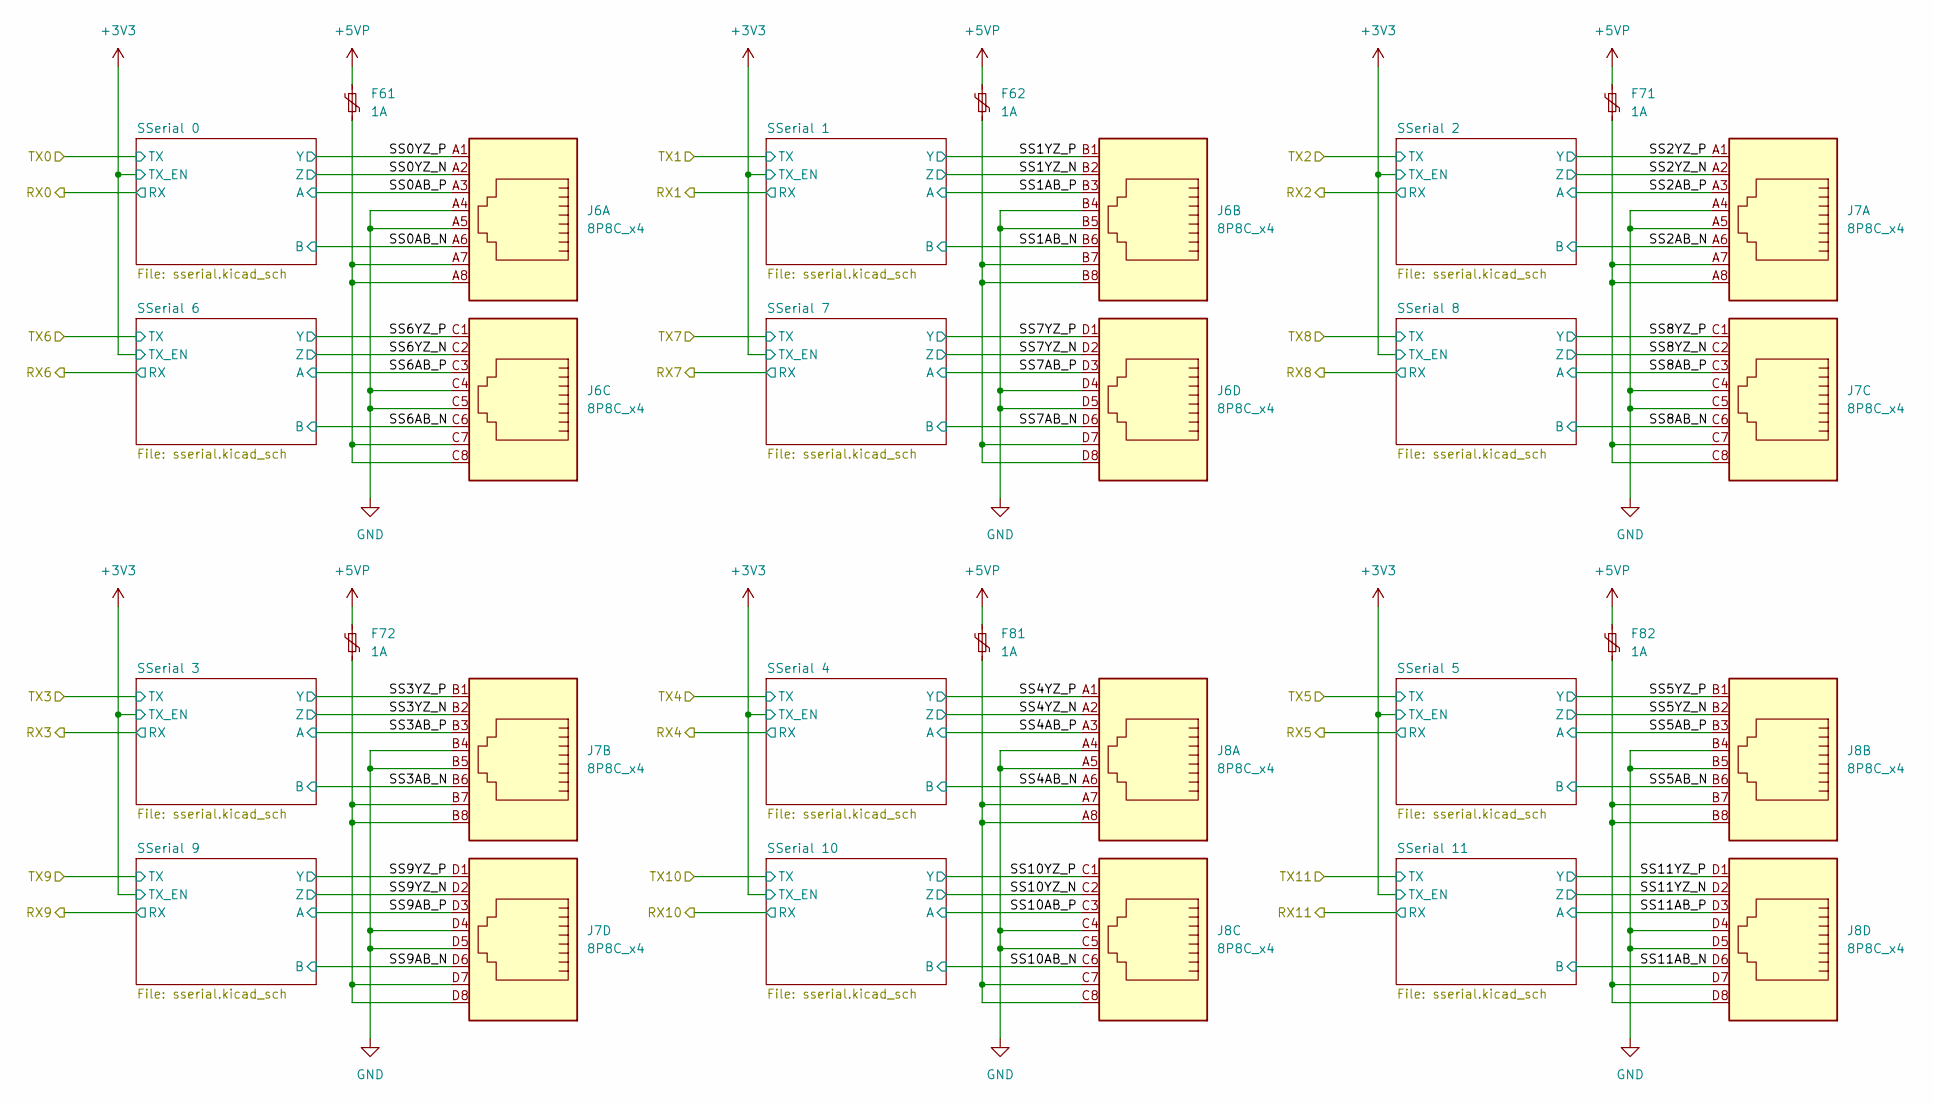
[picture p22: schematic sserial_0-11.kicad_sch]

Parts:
F61, F62, F71, F72, F81, F82: 1A; Fuse_1206_3216Metric
J6, J7, J8: 8P8C_x4; MJ5988-B022-HPRN1

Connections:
+5VP: F61.1, F62.1, F71.1, F72.1, F81.1, F82.1; also elsewhere on the board
/SSerial 0-11/SS0AB_N: J6.A6; also elsewhere on the board
/SSerial 0-11/SS0AB_P: J6.A3; also elsewhere on the board
/SSerial 0-11/SS0YZ_N: J6.A2; also elsewhere on the board
/SSerial 0-11/SS0YZ_P: J6.A1; also elsewhere on the board
/SSerial 0-11/SS1AB_N: J6.B6; also elsewhere on the board
/SSerial 0-11/SS1AB_P: J6.B3; also elsewhere on the board
/SSerial 0-11/SS1YZ_N: J6.B2; also elsewhere on the board
/SSerial 0-11/SS1YZ_P: J6.B1; also elsewhere on the board
/SSerial 0-11/SS2AB_N: J7.A6; also elsewhere on the board
/SSerial 0-11/SS2AB_P: J7.A3; also elsewhere on the board
/SSerial 0-11/SS2YZ_N: J7.A2; also elsewhere on the board
/SSerial 0-11/SS2YZ_P: J7.A1; also elsewhere on the board
/SSerial 0-11/SS3AB_N: J7.B6; also elsewhere on the board
/SSerial 0-11/SS3AB_P: J7.B3; also elsewhere on the board
/SSerial 0-11/SS3YZ_N: J7.B2; also elsewhere on the board
/SSerial 0-11/SS3YZ_P: J7.B1; also elsewhere on the board
/SSerial 0-11/SS4AB_N: J8.A6; also elsewhere on the board
/SSerial 0-11/SS4AB_P: J8.A3; also elsewhere on the board
/SSerial 0-11/SS4YZ_N: J8.A2; also elsewhere on the board
/SSerial 0-11/SS4YZ_P: J8.A1; also elsewhere on the board
/SSerial 0-11/SS5AB_N: J8.B6; also elsewhere on the board
/SSerial 0-11/SS5AB_P: J8.B3; also elsewhere on the board
/SSerial 0-11/SS5YZ_N: J8.B2; also elsewhere on the board
/SSerial 0-11/SS5YZ_P: J8.B1; also elsewhere on the board
/SSerial 0-11/SS6AB_N: J6.C6; also elsewhere on the board
/SSerial 0-11/SS6AB_P: J6.C3; also elsewhere on the board
/SSerial 0-11/SS6YZ_N: J6.C2; also elsewhere on the board
/SSerial 0-11/SS6YZ_P: J6.C1; also elsewhere on the board
/SSerial 0-11/SS7AB_N: J6.D6; also elsewhere on the board
/SSerial 0-11/SS7AB_P: J6.D3; also elsewhere on the board
/SSerial 0-11/SS7YZ_N: J6.D2; also elsewhere on the board
/SSerial 0-11/SS7YZ_P: J6.D1; also elsewhere on the board
/SSerial 0-11/SS8AB_N: J7.C6; also elsewhere on the board
/SSerial 0-11/SS8AB_P: J7.C3; also elsewhere on the board
/SSerial 0-11/SS8YZ_N: J7.C2; also elsewhere on the board
/SSerial 0-11/SS8YZ_P: J7.C1; also elsewhere on the board
/SSerial 0-11/SS9AB_N: J7.D6; also elsewhere on the board
/SSerial 0-11/SS9AB_P: J7.D3; also elsewhere on the board
/SSerial 0-11/SS9YZ_N: J7.D2; also elsewhere on the board
/SSerial 0-11/SS9YZ_P: J7.D1; also elsewhere on the board
/SSerial 0-11/SS10AB_N: J8.C6; also elsewhere on the board
/SSerial 0-11/SS10AB_P: J8.C3; also elsewhere on the board
/SSerial 0-11/SS10YZ_N: J8.C2; also elsewhere on the board
/SSerial 0-11/SS10YZ_P: J8.C1; also elsewhere on the board
/SSerial 0-11/SS11AB_N: J8.D6; also elsewhere on the board
/SSerial 0-11/SS11AB_P: J8.D3; also elsewhere on the board
/SSerial 0-11/SS11YZ_N: J8.D2; also elsewhere on the board
/SSerial 0-11/SS11YZ_P: J8.D1; also elsewhere on the board
GND: J6.A4, J6.A5, J6.B4, J6.B5, J6.C4, J6.C5, J6.D4, J6.D5, J7.A4, J7.A5, J7.B4, J7.B5, J7.C4, J7.C5, J7.D4, J7.D5, J8.A4, J8.A5, J8.B4, J8.B5, J8.C4, J8.C5, J8.D4, J8.D5; also elsewhere on the board
unnamed: F61.2, J6.A7, J6.A8, J6.C7, J6.C8
unnamed: F62.2, J6.B7, J6.B8, J6.D7, J6.D8
unnamed: F71.2, J7.A7, J7.A8, J7.C7, J7.C8
unnamed: F72.2, J7.B7, J7.B8, J7.D7, J7.D8
unnamed: F81.2, J8.A7, J8.A8, J8.C7, J8.C8
unnamed: F82.2, J8.B7, J8.B8, J8.D7, J8.D8

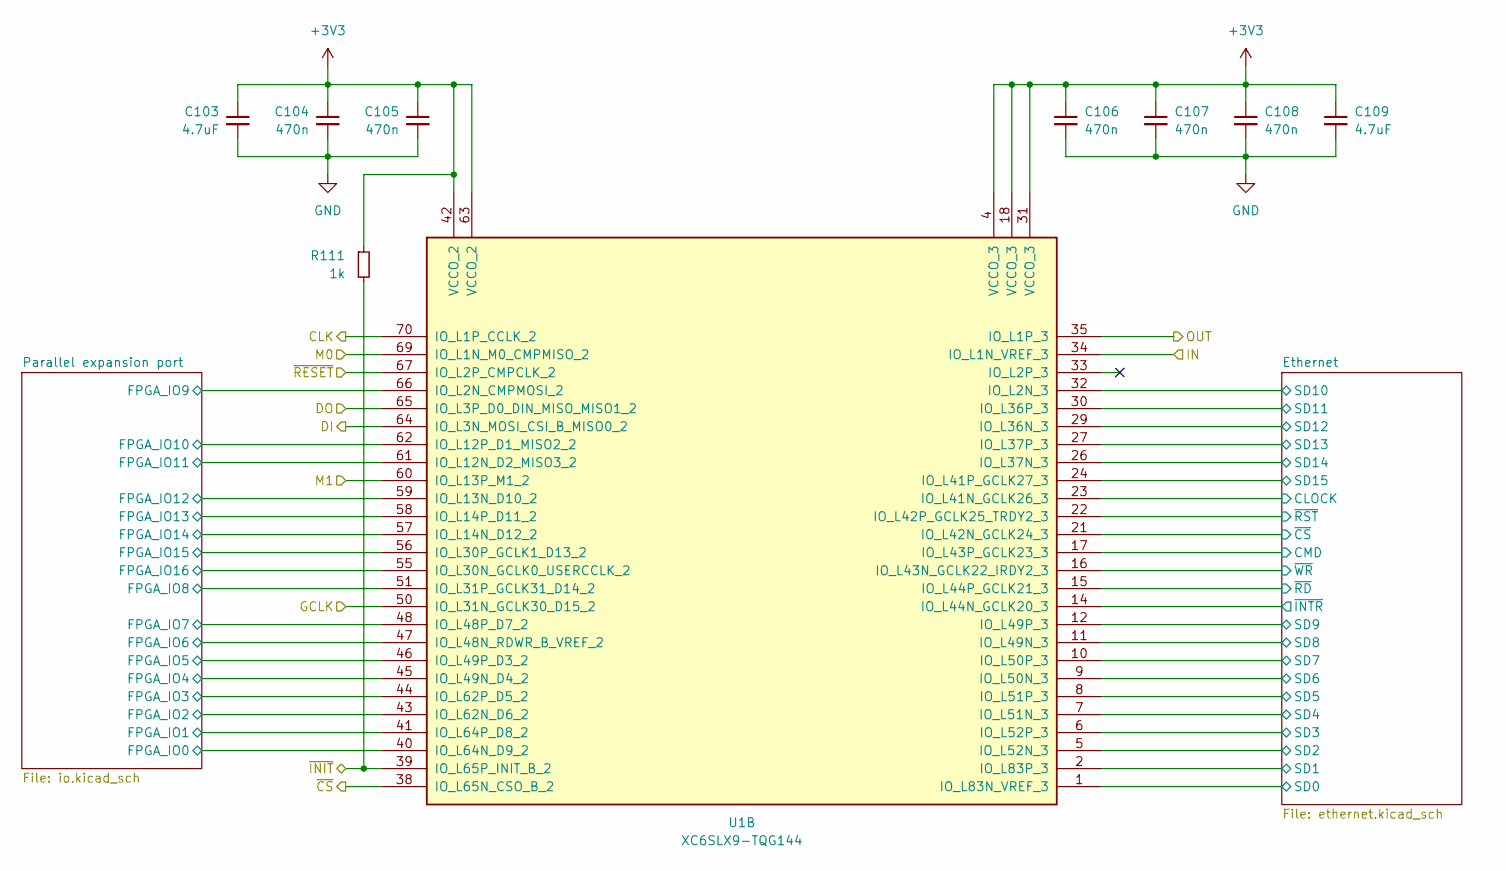
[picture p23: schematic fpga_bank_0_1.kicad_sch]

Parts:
C103, C109: 4.7uF; C_0603_1608Metric
C104, C105, C106, C107, C108: 470n; C_0603_1608Metric
R111: 1k; R_0603_1608Metric
U1: XC6SLX9-TQG144; TQFP-144_20x20mm_P0.5mm

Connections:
+3V3: C103.1, C104.1, C105.1, C106.1, C107.1, C108.1, C109.1, R111.1, U1.4 (VCCO_3), U1.18 (VCCO_3), U1.31 (VCCO_3), U1.42 (VCCO_2), U1.63 (VCCO_2); also elsewhere on the board
/FPGA Bank 0 1/CLK: U1.70 (IO_L1P_CCLK_2); also elsewhere on the board
/FPGA Bank 0 1/DI: U1.64 (IO_L3N_MOSI_CSI_B_MISO0_2); also elsewhere on the board
/FPGA Bank 0 1/DO: U1.65 (IO_L3P_D0_DIN_MISO_MISO1_2); also elsewhere on the board
/FPGA Bank 0 1/Ethernet/CLOCK: U1.23 (IO_L41N_GCLK26_3); also elsewhere on the board
/FPGA Bank 0 1/Ethernet/CMD: U1.17 (IO_L43P_GCLK23_3); also elsewhere on the board
/FPGA Bank 0 1/Ethernet/SD0: U1.1 (IO_L83N_VREF_3); also elsewhere on the board
/FPGA Bank 0 1/Ethernet/SD1: U1.2 (IO_L83P_3); also elsewhere on the board
/FPGA Bank 0 1/Ethernet/SD2: U1.5 (IO_L52N_3); also elsewhere on the board
/FPGA Bank 0 1/Ethernet/SD3: U1.6 (IO_L52P_3); also elsewhere on the board
/FPGA Bank 0 1/Ethernet/SD4: U1.7 (IO_L51N_3); also elsewhere on the board
/FPGA Bank 0 1/Ethernet/SD5: U1.8 (IO_L51P_3); also elsewhere on the board
/FPGA Bank 0 1/Ethernet/SD6: U1.9 (IO_L50N_3); also elsewhere on the board
/FPGA Bank 0 1/Ethernet/SD7: U1.10 (IO_L50P_3); also elsewhere on the board
/FPGA Bank 0 1/Ethernet/SD8: U1.11 (IO_L49N_3); also elsewhere on the board
/FPGA Bank 0 1/Ethernet/SD9: U1.12 (IO_L49P_3); also elsewhere on the board
/FPGA Bank 0 1/Ethernet/SD10: U1.32 (IO_L2N_3); also elsewhere on the board
/FPGA Bank 0 1/Ethernet/SD11: U1.30 (IO_L36P_3); also elsewhere on the board
/FPGA Bank 0 1/Ethernet/SD12: U1.29 (IO_L36N_3); also elsewhere on the board
/FPGA Bank 0 1/Ethernet/SD13: U1.27 (IO_L37P_3); also elsewhere on the board
/FPGA Bank 0 1/Ethernet/SD14: U1.26 (IO_L37N_3); also elsewhere on the board
/FPGA Bank 0 1/Ethernet/SD15: U1.24 (IO_L41P_GCLK27_3); also elsewhere on the board
/FPGA Bank 0 1/Ethernet/~CS: U1.21 (IO_L42N_GCLK24_3); also elsewhere on the board
/FPGA Bank 0 1/Ethernet/~INTR: U1.14 (IO_L44N_GCLK20_3); also elsewhere on the board
/FPGA Bank 0 1/Ethernet/~RD: U1.15 (IO_L44P_GCLK21_3); also elsewhere on the board
/FPGA Bank 0 1/Ethernet/~RST: U1.22 (IO_L42P_GCLK25_TRDY2_3); also elsewhere on the board
/FPGA Bank 0 1/Ethernet/~WR: U1.16 (IO_L43N_GCLK22_IRDY2_3); also elsewhere on the board
/FPGA Bank 0 1/GCLK: U1.50 (IO_L31N_GCLK30_D15_2); also elsewhere on the board
/FPGA Bank 0 1/IN: U1.34 (IO_L1N_VREF_3); also elsewhere on the board
/FPGA Bank 0 1/M0: U1.69 (IO_L1N_M0_CMPMISO_2); also elsewhere on the board
/FPGA Bank 0 1/M1: U1.60 (IO_L13P_M1_2); also elsewhere on the board
/FPGA Bank 0 1/OUT: U1.35 (IO_L1P_3); also elsewhere on the board
/FPGA Bank 0 1/Parallel expansion port/FPGA_IO0: U1.40 (IO_L64N_D9_2); also elsewhere on the board
/FPGA Bank 0 1/Parallel expansion port/FPGA_IO1: U1.41 (IO_L64P_D8_2); also elsewhere on the board
/FPGA Bank 0 1/Parallel expansion port/FPGA_IO2: U1.43 (IO_L62N_D6_2); also elsewhere on the board
/FPGA Bank 0 1/Parallel expansion port/FPGA_IO3: U1.44 (IO_L62P_D5_2); also elsewhere on the board
/FPGA Bank 0 1/Parallel expansion port/FPGA_IO4: U1.45 (IO_L49N_D4_2); also elsewhere on the board
/FPGA Bank 0 1/Parallel expansion port/FPGA_IO5: U1.46 (IO_L49P_D3_2); also elsewhere on the board
/FPGA Bank 0 1/Parallel expansion port/FPGA_IO6: U1.47 (IO_L48N_RDWR_B_VREF_2); also elsewhere on the board
/FPGA Bank 0 1/Parallel expansion port/FPGA_IO7: U1.48 (IO_L48P_D7_2); also elsewhere on the board
/FPGA Bank 0 1/Parallel expansion port/FPGA_IO8: U1.51 (IO_L31P_GCLK31_D14_2); also elsewhere on the board
/FPGA Bank 0 1/Parallel expansion port/FPGA_IO9: U1.66 (IO_L2N_CMPMOSI_2); also elsewhere on the board
/FPGA Bank 0 1/Parallel expansion port/FPGA_IO10: U1.62 (IO_L12P_D1_MISO2_2); also elsewhere on the board
/FPGA Bank 0 1/Parallel expansion port/FPGA_IO11: U1.61 (IO_L12N_D2_MISO3_2); also elsewhere on the board
/FPGA Bank 0 1/Parallel expansion port/FPGA_IO12: U1.59 (IO_L13N_D10_2); also elsewhere on the board
/FPGA Bank 0 1/Parallel expansion port/FPGA_IO13: U1.58 (IO_L14P_D11_2); also elsewhere on the board
/FPGA Bank 0 1/Parallel expansion port/FPGA_IO14: U1.57 (IO_L14N_D12_2); also elsewhere on the board
/FPGA Bank 0 1/Parallel expansion port/FPGA_IO15: U1.56 (IO_L30P_GCLK1_D13_2); also elsewhere on the board
/FPGA Bank 0 1/Parallel expansion port/FPGA_IO16: U1.55 (IO_L30N_GCLK0_USERCCLK_2); also elsewhere on the board
/FPGA Bank 0 1/~CS: U1.38 (IO_L65N_CSO_B_2); also elsewhere on the board
/FPGA Bank 0 1/~INIT: R111.2, U1.39 (IO_L65P_INIT_B_2); also elsewhere on the board
/FPGA Bank 0 1/~RESET: U1.67 (IO_L2P_CMPCLK_2); also elsewhere on the board
GND: C103.2, C104.2, C105.2, C106.2, C107.2, C108.2, C109.2; also elsewhere on the board

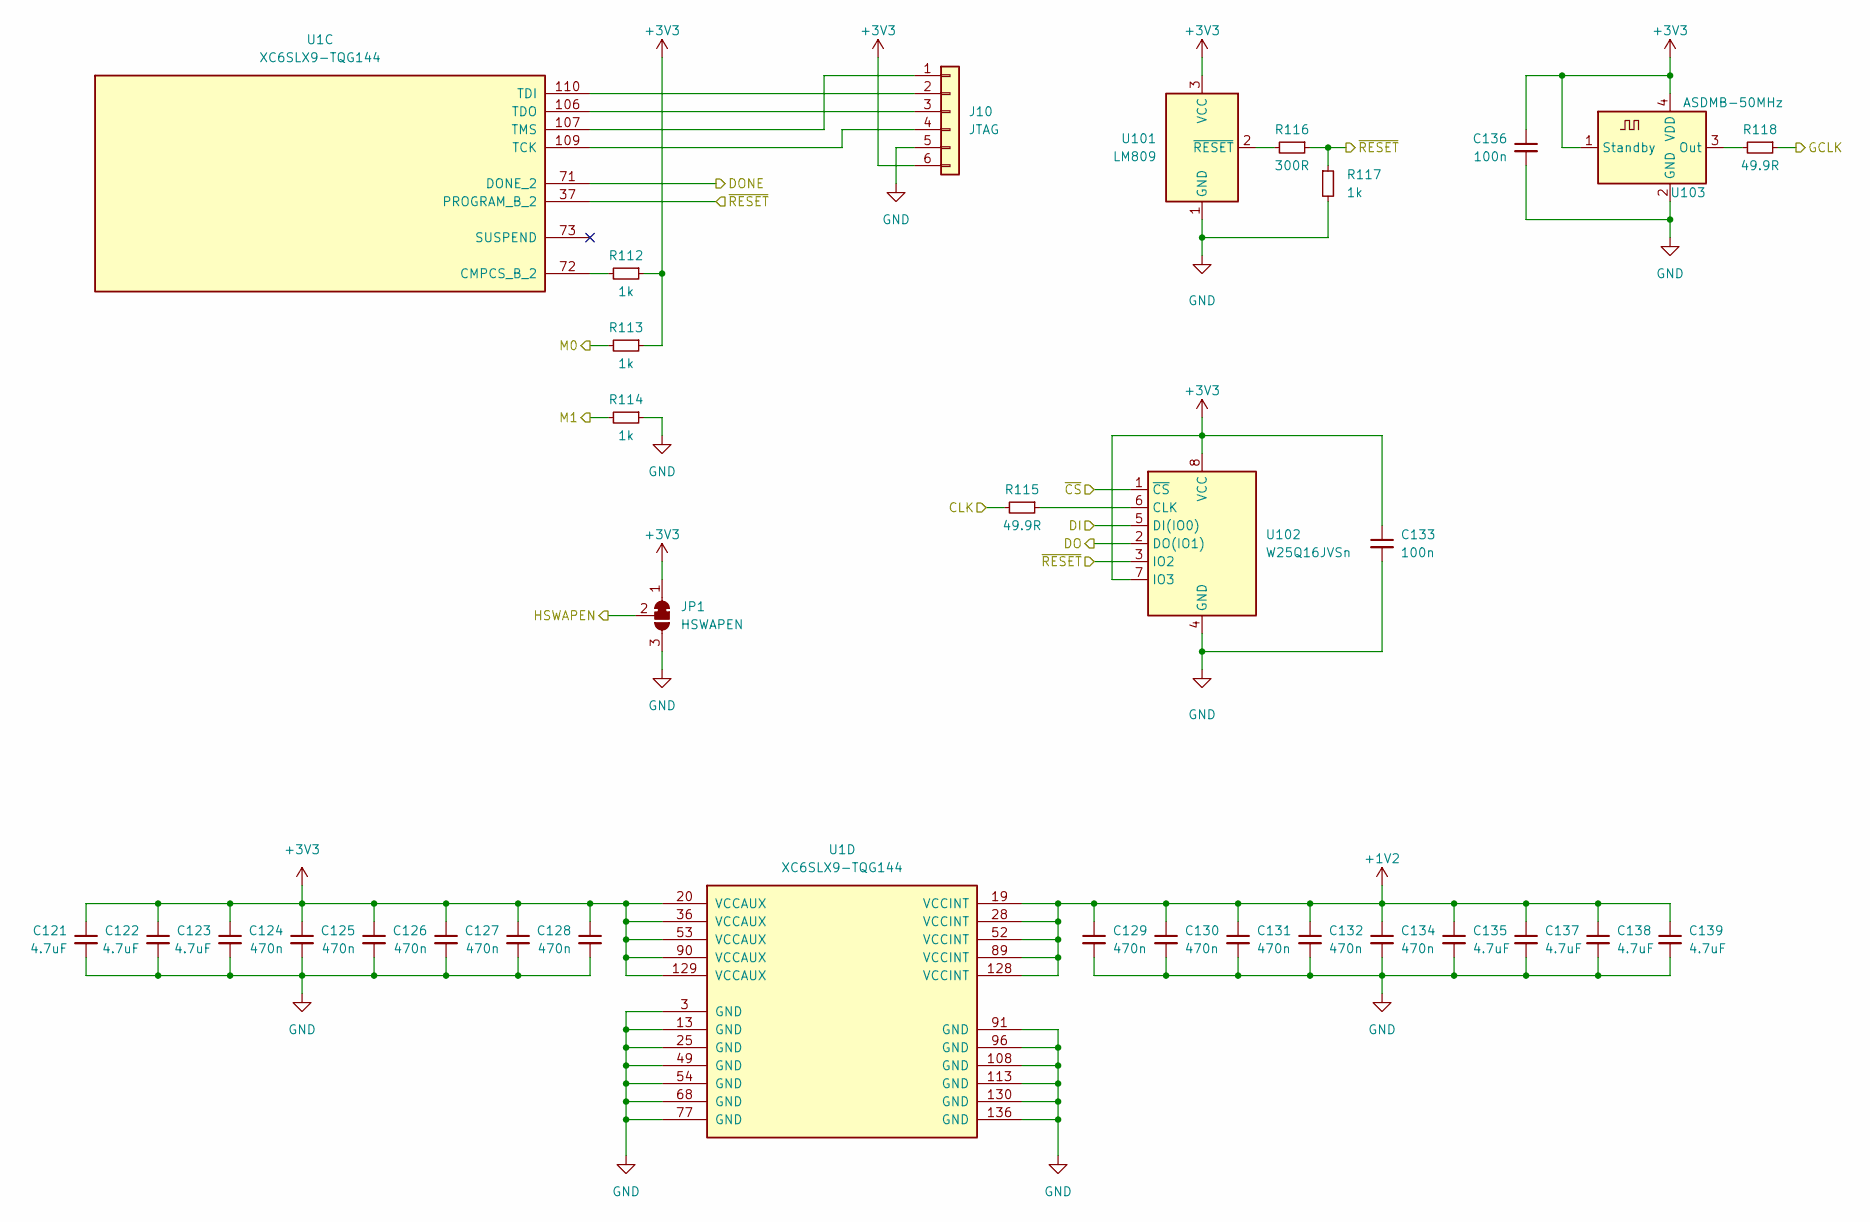
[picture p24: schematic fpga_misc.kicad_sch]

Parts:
C121, C122, C123, C135, C137, C138, C139: 4.7uF; C_0603_1608Metric
C124, C125, C126, C127, C128, C129, C130, C131, C132, C134: 470n; C_0603_1608Metric
C133, C136: 100n; C_0603_1608Metric
J10: JTAG; PinHeader_1x06_P2.54mm_Vertical_copy
JP1: HSWAPEN; SolderJumper-3_P1.3mm_Bridged12_RoundedPad1.0x1.5mm
R112, R113, R114, R117: 1k; R_0603_1608Metric
R115, R118: 49.9R; R_0603_1608Metric
R116: 300R; R_0603_1608Metric
U1: XC6SLX9-TQG144; TQFP-144_20x20mm_P0.5mm
U101: LM809; SOT-23
U102: W25Q16JVSn; SOIC-8_3.9x4.9mm_P1.27mm
U103: ASDMB-50MHz; Oscillator_SMD_Abracon_ASDMB-4Pin_2.5x2.0mm

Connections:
+1V2: C129.1, C130.1, C131.1, C132.1, C134.1, C135.1, C137.1, C138.1, C139.1, U1.19 (VCCINT), U1.28 (VCCINT), U1.52 (VCCINT), U1.89 (VCCINT), U1.128 (VCCINT); also elsewhere on the board
+3V3: C121.1, C122.1, C123.1, C124.1, C125.1, C126.1, C127.1, C128.1, C133.1, C136.1, J10.6, JP1.1 (A), R112.1, R113.1, U1.20 (VCCAUX), U1.36 (VCCAUX), U1.53 (VCCAUX), U1.90 (VCCAUX), U1.129 (VCCAUX), U101.3 (VCC), U102.7 (IO3), U102.8 (VCC), U103.1 (Standby), U103.4 (VDD); also elsewhere on the board
/FPGA Bank 0 1/CLK: R115.2; also elsewhere on the board
/FPGA Bank 0 1/DI: U102.5 (DI(IO0)); also elsewhere on the board
/FPGA Bank 0 1/DO: U102.2 (DO(IO1)); also elsewhere on the board
/FPGA Bank 0 1/GCLK: R118.1; also elsewhere on the board
/FPGA Bank 0 1/M0: R113.2; also elsewhere on the board
/FPGA Bank 0 1/M1: R114.2; also elsewhere on the board
/FPGA Bank 0 1/~CS: U102.1 (~CS); also elsewhere on the board
/FPGA Bank 0 1/~RESET: R116.1, R117.1, U1.37 (PROGRAM_B_2), U102.3 (IO2); also elsewhere on the board
/FPGA Bank 2 3/HSWAPEN: JP1.2 (C); also elsewhere on the board
/FPGA Misc/DONE: U1.71 (DONE_2); also elsewhere on the board
GND: C121.2, C122.2, C123.2, C124.2, C125.2, C126.2, C127.2, C128.2, C129.2, C130.2, C131.2, C132.2, C133.2, C134.2, C135.2, C136.2, C137.2, C138.2, C139.2, J10.5, JP1.3 (B), R114.1, R117.2, U1.3 (GND), U1.13 (GND), U1.25 (GND), U1.49 (GND), U1.54 (GND), U1.68 (GND), U1.77 (GND), U1.91 (GND), U1.96 (GND), U1.108 (GND), U1.113 (GND), U1.130 (GND), U1.136 (GND), U101.1 (GND), U102.4 (GND), U103.2 (GND); also elsewhere on the board
unnamed: J10.1, U1.107 (TMS)
unnamed: J10.2, U1.110 (TDI)
unnamed: J10.3, U1.106 (TDO)
unnamed: J10.4, U1.109 (TCK)
unnamed: R112.2, U1.72 (CMPCS_B_2)
unnamed: R116.2, U101.2 (~RESET)
unnamed: R115.1, U102.6 (CLK)
unnamed: R118.2, U103.3 (Out)

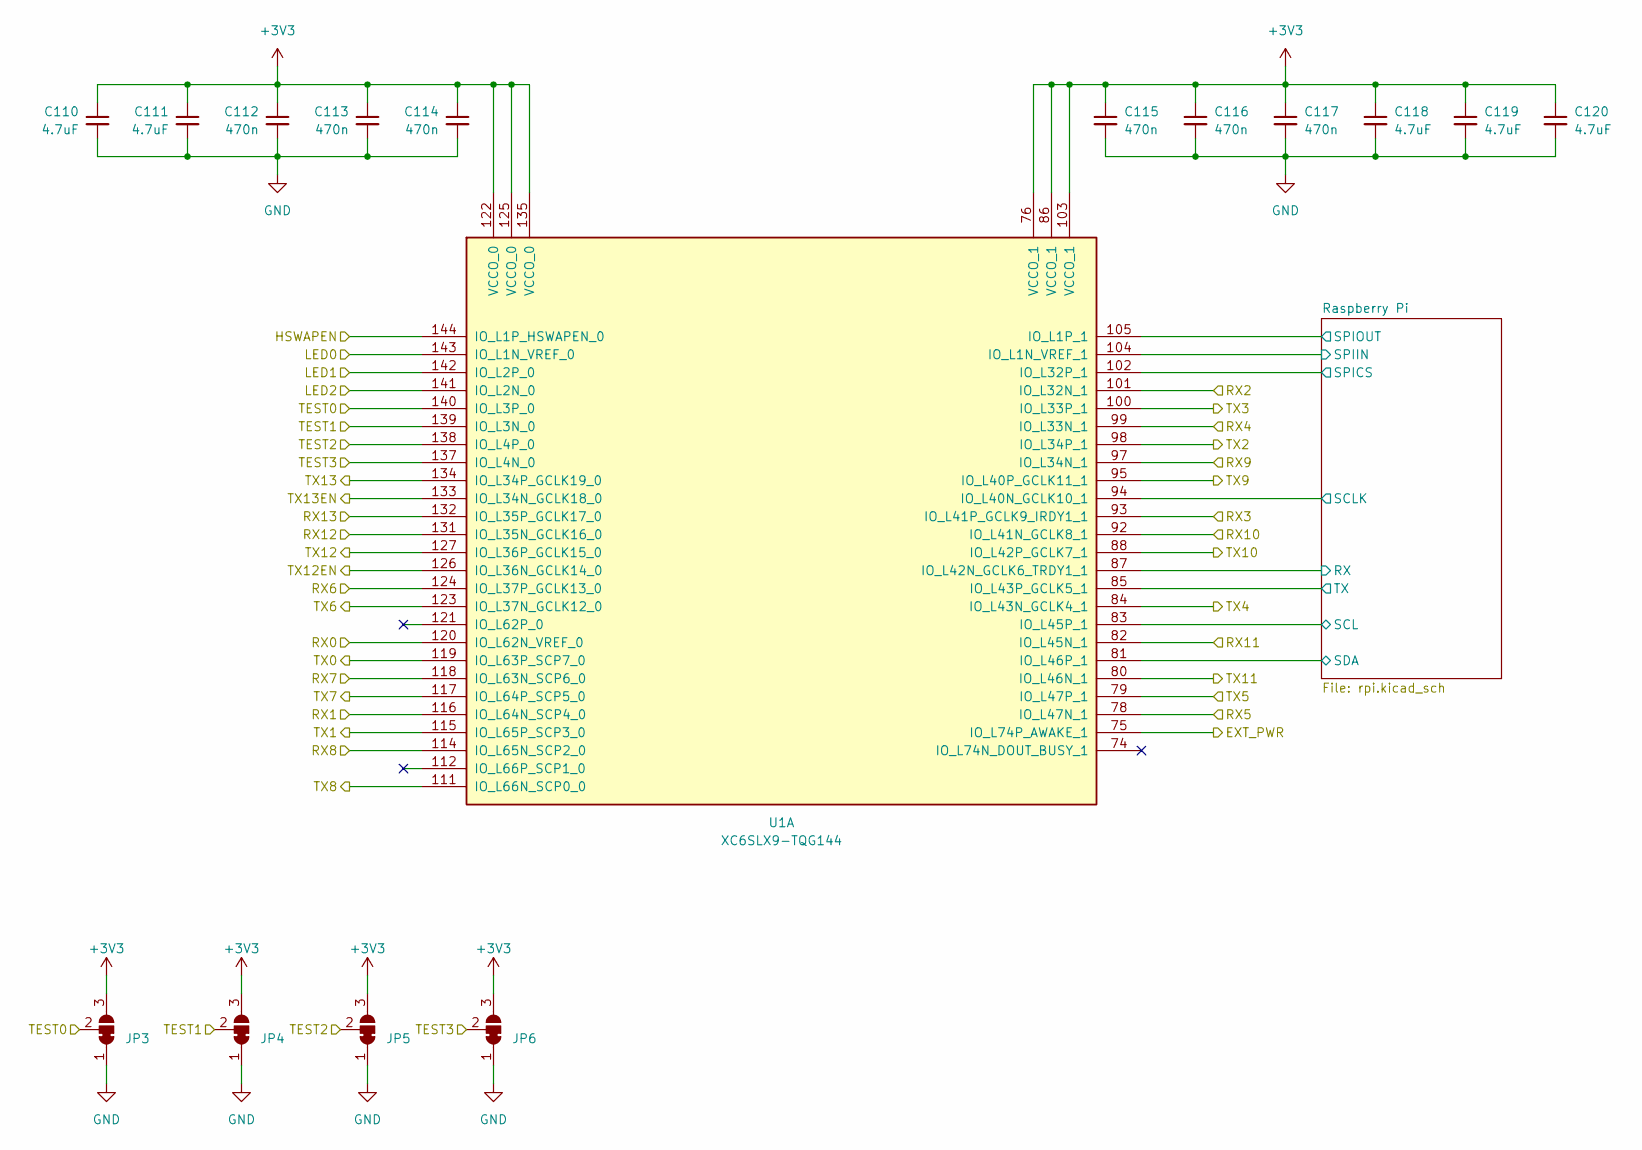
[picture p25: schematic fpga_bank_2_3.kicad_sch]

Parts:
C110, C111, C118, C119, C120: 4.7uF; C_0603_1608Metric
C112, C113, C114, C115, C116, C117: 470n; C_0603_1608Metric
JP3, JP4, JP5, JP6: SolderJumper-3_P1.3mm_Open_RoundedPad1.0x1.5mm
U1: XC6SLX9-TQG144; TQFP-144_20x20mm_P0.5mm

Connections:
+3V3: C110.1, C111.1, C112.1, C113.1, C114.1, C115.1, C116.1, C117.1, C118.1, C119.1, C120.1, JP3.3 (B), JP4.3 (B), JP5.3 (B), JP6.3 (B), U1.76 (VCCO_1), U1.86 (VCCO_1), U1.103 (VCCO_1), U1.122 (VCCO_0), U1.125 (VCCO_0), U1.135 (VCCO_0); also elsewhere on the board
/FPGA Bank 2 3/EXT_PWR: U1.75 (IO_L74P_AWAKE_1); also elsewhere on the board
/FPGA Bank 2 3/HSWAPEN: U1.144 (IO_L1P_HSWAPEN_0); also elsewhere on the board
/FPGA Bank 2 3/LED0: U1.143 (IO_L1N_VREF_0); also elsewhere on the board
/FPGA Bank 2 3/LED1: U1.142 (IO_L2P_0); also elsewhere on the board
/FPGA Bank 2 3/LED2: U1.141 (IO_L2N_0); also elsewhere on the board
/FPGA Bank 2 3/RX0: U1.120 (IO_L62N_VREF_0); also elsewhere on the board
/FPGA Bank 2 3/RX1: U1.116 (IO_L64N_SCP4_0); also elsewhere on the board
/FPGA Bank 2 3/RX2: U1.101 (IO_L32N_1); also elsewhere on the board
/FPGA Bank 2 3/RX3: U1.93 (IO_L41P_GCLK9_IRDY1_1); also elsewhere on the board
/FPGA Bank 2 3/RX4: U1.99 (IO_L33N_1); also elsewhere on the board
/FPGA Bank 2 3/RX5: U1.78 (IO_L47N_1); also elsewhere on the board
/FPGA Bank 2 3/RX6: U1.124 (IO_L37P_GCLK13_0); also elsewhere on the board
/FPGA Bank 2 3/RX7: U1.118 (IO_L63N_SCP6_0); also elsewhere on the board
/FPGA Bank 2 3/RX8: U1.114 (IO_L65N_SCP2_0); also elsewhere on the board
/FPGA Bank 2 3/RX9: U1.97 (IO_L34N_1); also elsewhere on the board
/FPGA Bank 2 3/RX10: U1.92 (IO_L41N_GCLK8_1); also elsewhere on the board
/FPGA Bank 2 3/RX11: U1.82 (IO_L45N_1); also elsewhere on the board
/FPGA Bank 2 3/RX12: U1.131 (IO_L35N_GCLK16_0); also elsewhere on the board
/FPGA Bank 2 3/RX13: U1.132 (IO_L35P_GCLK17_0); also elsewhere on the board
/FPGA Bank 2 3/Raspberry Pi/RX: U1.87 (IO_L42N_GCLK6_TRDY1_1); also elsewhere on the board
/FPGA Bank 2 3/Raspberry Pi/SCL: U1.83 (IO_L45P_1); also elsewhere on the board
/FPGA Bank 2 3/Raspberry Pi/SCLK: U1.94 (IO_L40N_GCLK10_1); also elsewhere on the board
/FPGA Bank 2 3/Raspberry Pi/SDA: U1.81 (IO_L46P_1); also elsewhere on the board
/FPGA Bank 2 3/Raspberry Pi/SPICS: U1.102 (IO_L32P_1); also elsewhere on the board
/FPGA Bank 2 3/Raspberry Pi/SPIIN: U1.104 (IO_L1N_VREF_1); also elsewhere on the board
/FPGA Bank 2 3/Raspberry Pi/SPIOUT: U1.105 (IO_L1P_1); also elsewhere on the board
/FPGA Bank 2 3/Raspberry Pi/TX: U1.85 (IO_L43P_GCLK5_1); also elsewhere on the board
/FPGA Bank 2 3/TEST0: JP3.2 (C), U1.140 (IO_L3P_0); also elsewhere on the board
/FPGA Bank 2 3/TEST1: JP4.2 (C), U1.139 (IO_L3N_0); also elsewhere on the board
/FPGA Bank 2 3/TEST2: JP5.2 (C), U1.138 (IO_L4P_0); also elsewhere on the board
/FPGA Bank 2 3/TEST3: JP6.2 (C), U1.137 (IO_L4N_0); also elsewhere on the board
/FPGA Bank 2 3/TX0: U1.119 (IO_L63P_SCP7_0); also elsewhere on the board
/FPGA Bank 2 3/TX1: U1.115 (IO_L65P_SCP3_0); also elsewhere on the board
/FPGA Bank 2 3/TX2: U1.98 (IO_L34P_1); also elsewhere on the board
/FPGA Bank 2 3/TX3: U1.100 (IO_L33P_1); also elsewhere on the board
/FPGA Bank 2 3/TX4: U1.84 (IO_L43N_GCLK4_1); also elsewhere on the board
/FPGA Bank 2 3/TX5: U1.79 (IO_L47P_1); also elsewhere on the board
/FPGA Bank 2 3/TX6: U1.123 (IO_L37N_GCLK12_0); also elsewhere on the board
/FPGA Bank 2 3/TX7: U1.117 (IO_L64P_SCP5_0); also elsewhere on the board
/FPGA Bank 2 3/TX8: U1.111 (IO_L66N_SCP0_0); also elsewhere on the board
/FPGA Bank 2 3/TX9: U1.95 (IO_L40P_GCLK11_1); also elsewhere on the board
/FPGA Bank 2 3/TX10: U1.88 (IO_L42P_GCLK7_1); also elsewhere on the board
/FPGA Bank 2 3/TX11: U1.80 (IO_L46N_1); also elsewhere on the board
/FPGA Bank 2 3/TX12: U1.127 (IO_L36P_GCLK15_0); also elsewhere on the board
/FPGA Bank 2 3/TX12EN: U1.126 (IO_L36N_GCLK14_0); also elsewhere on the board
/FPGA Bank 2 3/TX13: U1.134 (IO_L34P_GCLK19_0); also elsewhere on the board
/FPGA Bank 2 3/TX13EN: U1.133 (IO_L34N_GCLK18_0); also elsewhere on the board
GND: C110.2, C111.2, C112.2, C113.2, C114.2, C115.2, C116.2, C117.2, C118.2, C119.2, C120.2, JP3.1 (A), JP4.1 (A), JP5.1 (A), JP6.1 (A); also elsewhere on the board

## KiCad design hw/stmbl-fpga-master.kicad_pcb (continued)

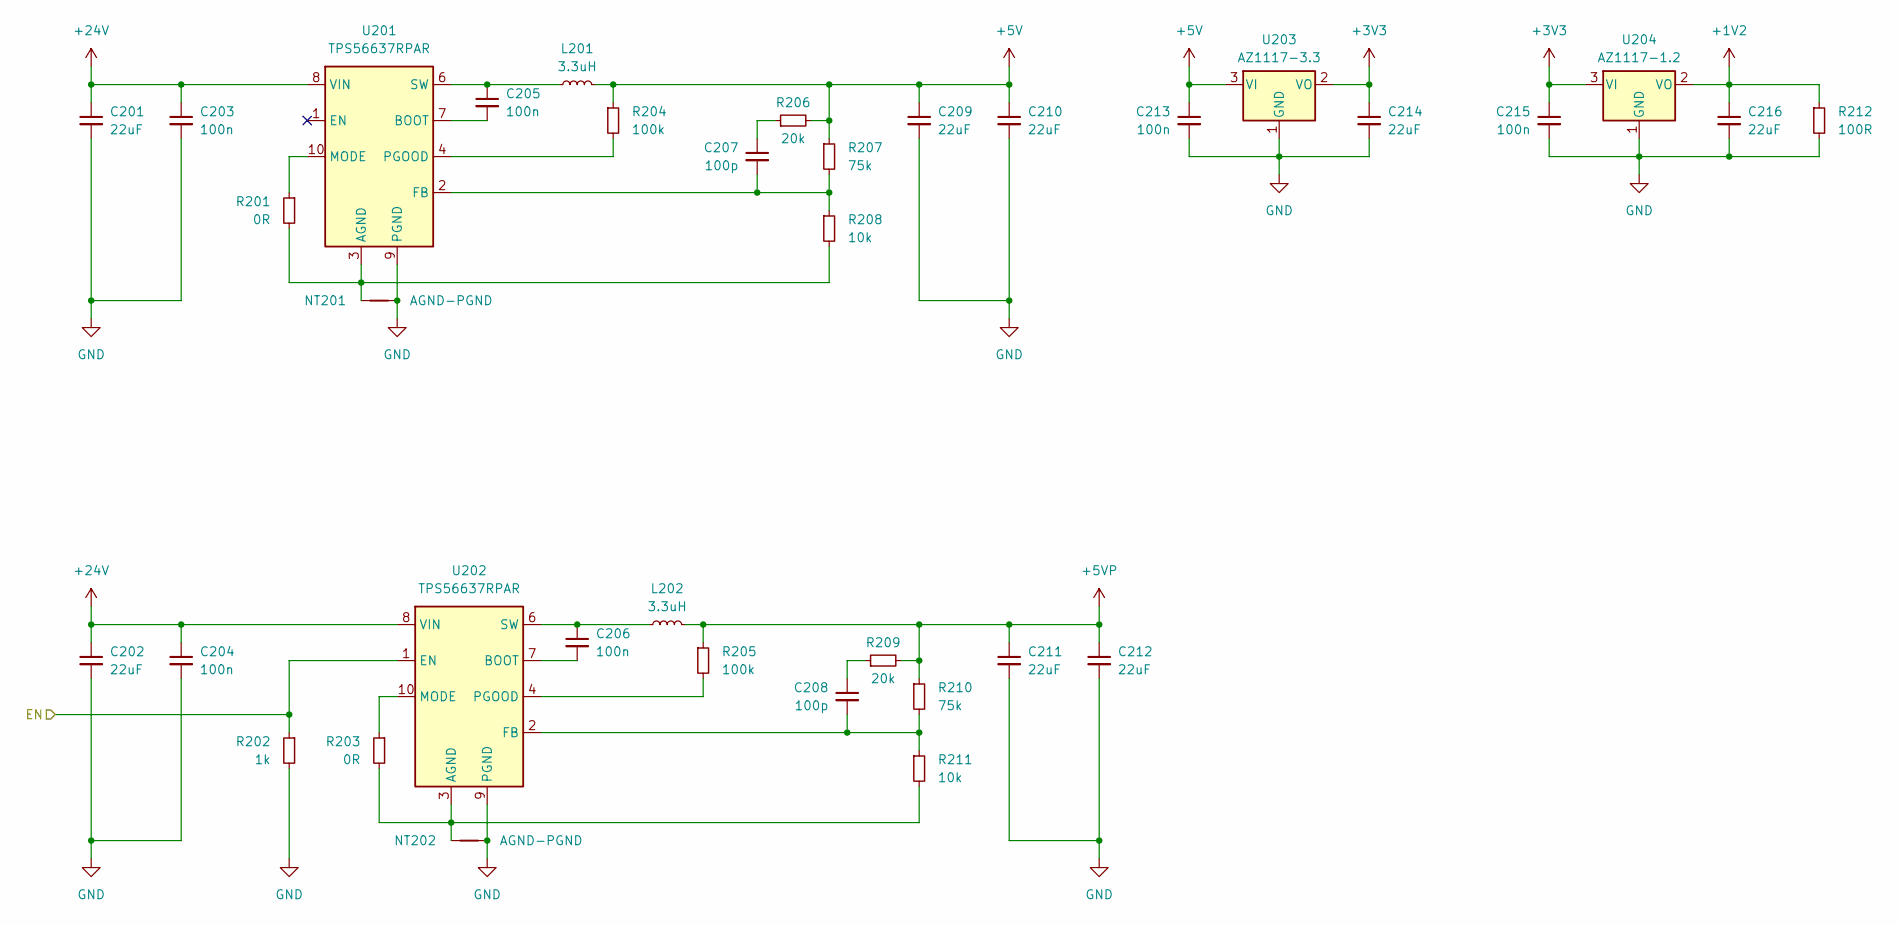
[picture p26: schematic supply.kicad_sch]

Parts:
C201, C202, C209, C210, C211, C212, C214, C216: 22uF; C_1206_3216Metric
C203, C204, C205, C206, C213, C215: 100n; C_0603_1608Metric
C207, C208: 100p; C_0603_1608Metric
L201, L202: 3.3uH; L_Sunlord_MWSA0603S
NT201, NT202: AGND-PGND; NetTie-2_SMD_Pad0.5mm
R201, R203: 0R; R_0603_1608Metric
R202: 1k; R_0603_1608Metric
R204, R205: 100k; R_0603_1608Metric
R206, R209: 20k; R_0603_1608Metric
R207, R210: 75k; R_0603_1608Metric
R208, R211: 10k; R_0603_1608Metric
R212: 100R; R_0603_1608Metric
U201, U202: TPS56637RPAR; Texas_RPA0010A_VQFN-HR-10_3x3mm_P0.5mm
U203: AZ1117-3.3; SOT-223-3_TabPin2
U204: AZ1117-1.2; SOT-223-3_TabPin2

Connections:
+1V2: C216.1, R212.1, U204.2 (VO); also elsewhere on the board
+3V3: C214.1, C215.1, U203.2 (VO), U204.3 (VI); also elsewhere on the board
+5V: C209.1, C210.1, C213.1, L201.2, R204.1, R206.2, R207.1, U203.3 (VI); also elsewhere on the board
+5VP: C211.1, C212.1, L202.2, R205.1, R209.2, R210.1; also elsewhere on the board
+24V: C201.1, C202.1, C203.1, C204.1, U201.8 (VIN), U202.8 (VIN); also elsewhere on the board
/FPGA Bank 2 3/EXT_PWR: R202.1, U202.1 (EN); also elsewhere on the board
GND: C201.2, C202.2, C203.2, C204.2, C209.2, C210.2, C211.2, C212.2, C213.2, C214.2, C215.2, C216.2, NT201.2, NT202.2, R202.2, R212.2, U201.9 (PGND), U202.9 (PGND), U203.1 (GND), U204.1 (GND); also elsewhere on the board
unnamed: C207.1, R206.1
unnamed: C208.1, R209.1
unnamed: NT201.1, R201.2, R208.2, U201.3 (AGND)
unnamed: C205.2, U201.7 (BOOT)
unnamed: C207.2, R207.2, R208.1, U201.2 (FB)
unnamed: R201.1, U201.10 (MODE)
unnamed: R204.2, U201.4 (PGOOD)
unnamed: C205.1, L201.1, U201.6 (SW)
unnamed: NT202.1, R203.2, R211.2, U202.3 (AGND)
unnamed: C206.2, U202.7 (BOOT)
unnamed: C208.2, R210.2, R211.1, U202.2 (FB)
unnamed: R203.1, U202.10 (MODE)
unnamed: R205.2, U202.4 (PGOOD)
unnamed: C206.1, L202.1, U202.6 (SW)

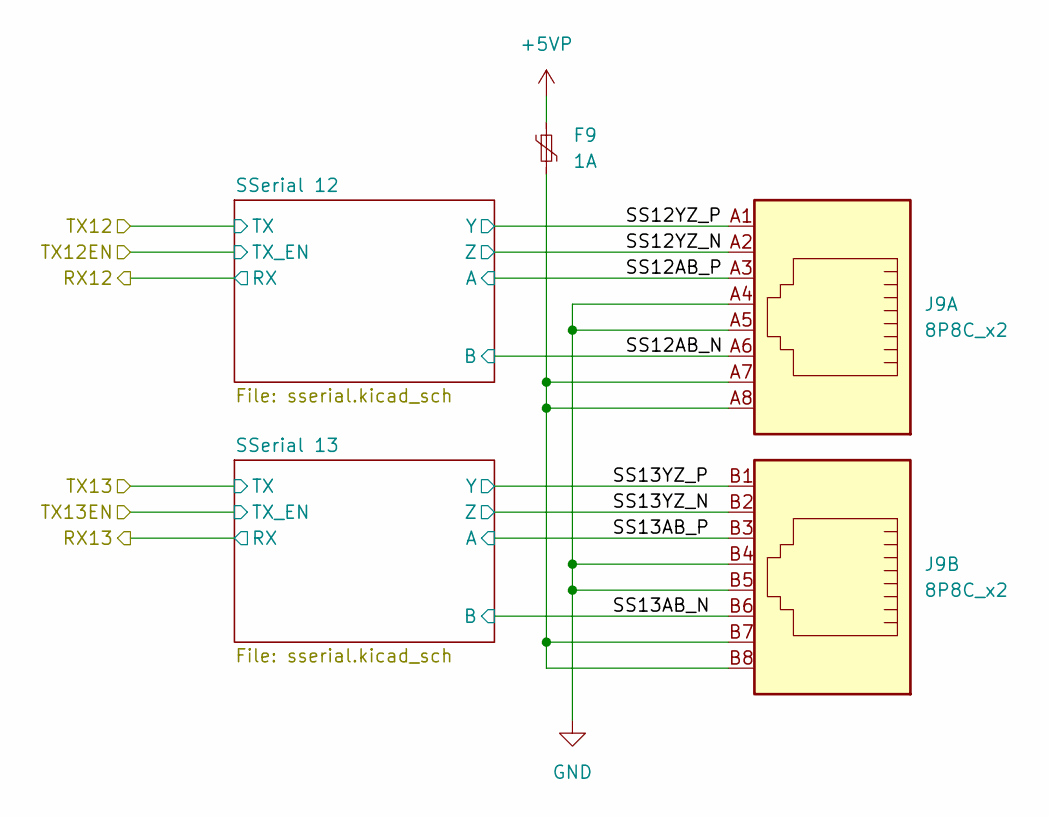
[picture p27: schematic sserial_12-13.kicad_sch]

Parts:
F9: 1A; Fuse_1206_3216Metric
J9: 8P8C_x2; HC-RJ45-5622-2-6

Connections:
+5VP: F9.1; also elsewhere on the board
/SSerial 12-13/SS12AB_N: J9.A6; also elsewhere on the board
/SSerial 12-13/SS12AB_P: J9.A3; also elsewhere on the board
/SSerial 12-13/SS12YZ_N: J9.A2; also elsewhere on the board
/SSerial 12-13/SS12YZ_P: J9.A1; also elsewhere on the board
/SSerial 12-13/SS13AB_N: J9.B6; also elsewhere on the board
/SSerial 12-13/SS13AB_P: J9.B3; also elsewhere on the board
/SSerial 12-13/SS13YZ_N: J9.B2; also elsewhere on the board
/SSerial 12-13/SS13YZ_P: J9.B1; also elsewhere on the board
GND: J9.A4, J9.A5, J9.B4, J9.B5; also elsewhere on the board
unnamed: F9.2, J9.A7, J9.A8, J9.B7, J9.B8

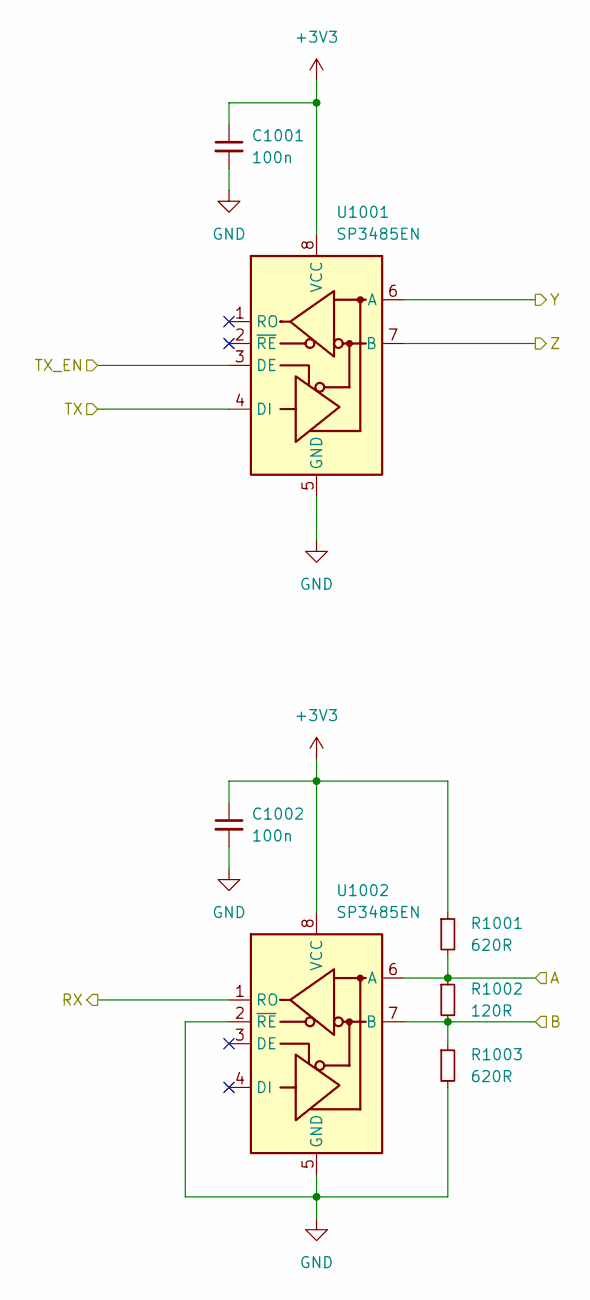
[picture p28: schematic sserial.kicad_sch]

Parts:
C1001, C1002: 100n; C_0603_1608Metric
R1001, R1003: 620R; R_0603_1608Metric
R1002: 120R; R_0603_1608Metric
U1001, U1002: SP3485EN; SOIC-8_3.9x4.9mm_P1.27mm

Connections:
+3V3: C1001.1, C1002.1, R1001.1, U1001.3 (DE), U1001.8 (VCC), U1002.8 (VCC); also elsewhere on the board
/FPGA Bank 2 3/RX0: U1002.1 (RO); also elsewhere on the board
/FPGA Bank 2 3/TX0: U1001.4 (DI); also elsewhere on the board
/SSerial 0-11/SS0AB_N: R1002.2, R1003.1, U1002.7 (B); also elsewhere on the board
/SSerial 0-11/SS0AB_P: R1001.2, R1002.1, U1002.6 (A); also elsewhere on the board
/SSerial 0-11/SS0YZ_N: U1001.7 (B); also elsewhere on the board
/SSerial 0-11/SS0YZ_P: U1001.6 (A); also elsewhere on the board
GND: C1001.2, C1002.2, R1003.2, U1001.5 (GND), U1002.2 (~RE), U1002.5 (GND); also elsewhere on the board

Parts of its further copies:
C1101, C1102, C1201, C1202, C1301, C1302, C1401, C1402, C1501, C1502, C1601, C1602, C1701, C1702, C1801, C1802, C1901, C1902, C2001, C2002, C2101, C2102, C2201, C2202, C2301, C2302: 100n; C_0603_1608Metric
R1101, R1103, R1201, R1203, R1301, R1303, R1401, R1403, R1501, R1503, R1601, R1603, R1701, R1703, R1801, R1803, R1901, R1903, R2001, R2003, R2101, R2103, R2201, R2203, R2301, R2303: 620R; R_0603_1608Metric
R1102, R1202, R1302, R1402, R1502, R1602, R1702, R1802, R1902, R2002, R2102, R2202, R2302: 120R; R_0603_1608Metric
U1101, U1102, U1201, U1202, U1301, U1302, U1401, U1402, U1501, U1502, U1601, U1602, U1701, U1702, U1801, U1802, U1901, U1902, U2001, U2002, U2101, U2102, U2201, U2202, U2301, U2302: SP3485EN; SOIC-8_3.9x4.9mm_P1.27mm

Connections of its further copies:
+3V3: C1101.1, C1102.1, C1201.1, C1202.1, C1301.1, C1302.1, C1401.1, C1402.1, C1501.1, C1502.1, C1601.1, C1602.1, C1701.1, C1702.1, C1801.1, C1802.1, C1901.1, C1902.1, C2001.1, C2002.1, C2101.1, C2102.1, C2201.1, C2202.1, C2301.1, C2302.1, R1101.1, R1201.1, R1301.1, R1401.1, R1501.1, R1601.1, R1701.1, R1801.1, R1901.1, R2001.1, R2101.1, R2201.1, R2301.1, U1101.3 (DE), U1101.8 (VCC), U1102.8 (VCC), U1201.3 (DE), U1201.8 (VCC), U1202.8 (VCC), U1301.3 (DE), U1301.8 (VCC), U1302.8 (VCC), U1401.3 (DE), U1401.8 (VCC), U1402.8 (VCC), U1501.3 (DE), U1501.8 (VCC), U1502.8 (VCC), U1601.3 (DE), U1601.8 (VCC), U1602.8 (VCC), U1701.3 (DE), U1701.8 (VCC), U1702.8 (VCC), U1801.3 (DE), U1801.8 (VCC), U1802.8 (VCC), U1901.3 (DE), U1901.8 (VCC), U1902.8 (VCC), U2001.3 (DE), U2001.8 (VCC), U2002.8 (VCC), U2101.3 (DE), U2101.8 (VCC), U2102.8 (VCC), U2201.8 (VCC), U2202.8 (VCC), U2301.8 (VCC), U2302.8 (VCC); also elsewhere on the board
/FPGA Bank 2 3/RX1: U1102.1 (RO); also elsewhere on the board
/FPGA Bank 2 3/RX2: U1202.1 (RO); also elsewhere on the board
/FPGA Bank 2 3/RX3: U1302.1 (RO); also elsewhere on the board
/FPGA Bank 2 3/RX4: U1402.1 (RO); also elsewhere on the board
/FPGA Bank 2 3/RX5: U1502.1 (RO); also elsewhere on the board
/FPGA Bank 2 3/RX6: U1602.1 (RO); also elsewhere on the board
/FPGA Bank 2 3/RX7: U1702.1 (RO); also elsewhere on the board
/FPGA Bank 2 3/RX8: U1802.1 (RO); also elsewhere on the board
/FPGA Bank 2 3/RX9: U1902.1 (RO); also elsewhere on the board
/FPGA Bank 2 3/RX10: U2002.1 (RO); also elsewhere on the board
/FPGA Bank 2 3/RX11: U2102.1 (RO); also elsewhere on the board
/FPGA Bank 2 3/RX12: U2202.1 (RO); also elsewhere on the board
/FPGA Bank 2 3/RX13: U2302.1 (RO); also elsewhere on the board
/FPGA Bank 2 3/TX1: U1101.4 (DI); also elsewhere on the board
/FPGA Bank 2 3/TX2: U1201.4 (DI); also elsewhere on the board
/FPGA Bank 2 3/TX3: U1301.4 (DI); also elsewhere on the board
/FPGA Bank 2 3/TX4: U1401.4 (DI); also elsewhere on the board
/FPGA Bank 2 3/TX5: U1501.4 (DI); also elsewhere on the board
/FPGA Bank 2 3/TX6: U1601.4 (DI); also elsewhere on the board
/FPGA Bank 2 3/TX7: U1701.4 (DI); also elsewhere on the board
/FPGA Bank 2 3/TX8: U1801.4 (DI); also elsewhere on the board
/FPGA Bank 2 3/TX9: U1901.4 (DI); also elsewhere on the board
/FPGA Bank 2 3/TX10: U2001.4 (DI); also elsewhere on the board
/FPGA Bank 2 3/TX11: U2101.4 (DI); also elsewhere on the board
/FPGA Bank 2 3/TX12: U2201.4 (DI); also elsewhere on the board
/FPGA Bank 2 3/TX12EN: U2201.3 (DE); also elsewhere on the board
/FPGA Bank 2 3/TX13: U2301.4 (DI); also elsewhere on the board
/FPGA Bank 2 3/TX13EN: U2301.3 (DE); also elsewhere on the board
/SSerial 0-11/SS1AB_N: R1102.2, R1103.1, U1102.7 (B); also elsewhere on the board
/SSerial 0-11/SS1AB_P: R1101.2, R1102.1, U1102.6 (A); also elsewhere on the board
/SSerial 0-11/SS1YZ_N: U1101.7 (B); also elsewhere on the board
/SSerial 0-11/SS1YZ_P: U1101.6 (A); also elsewhere on the board
/SSerial 0-11/SS2AB_N: R1202.2, R1203.1, U1202.7 (B); also elsewhere on the board
/SSerial 0-11/SS2AB_P: R1201.2, R1202.1, U1202.6 (A); also elsewhere on the board
/SSerial 0-11/SS2YZ_N: U1201.7 (B); also elsewhere on the board
/SSerial 0-11/SS2YZ_P: U1201.6 (A); also elsewhere on the board
/SSerial 0-11/SS3AB_N: R1302.2, R1303.1, U1302.7 (B); also elsewhere on the board
/SSerial 0-11/SS3AB_P: R1301.2, R1302.1, U1302.6 (A); also elsewhere on the board
/SSerial 0-11/SS3YZ_N: U1301.7 (B); also elsewhere on the board
/SSerial 0-11/SS3YZ_P: U1301.6 (A); also elsewhere on the board
/SSerial 0-11/SS4AB_N: R1402.2, R1403.1, U1402.7 (B); also elsewhere on the board
/SSerial 0-11/SS4AB_P: R1401.2, R1402.1, U1402.6 (A); also elsewhere on the board
/SSerial 0-11/SS4YZ_N: U1401.7 (B); also elsewhere on the board
/SSerial 0-11/SS4YZ_P: U1401.6 (A); also elsewhere on the board
/SSerial 0-11/SS5AB_N: R1502.2, R1503.1, U1502.7 (B); also elsewhere on the board
/SSerial 0-11/SS5AB_P: R1501.2, R1502.1, U1502.6 (A); also elsewhere on the board
/SSerial 0-11/SS5YZ_N: U1501.7 (B); also elsewhere on the board
/SSerial 0-11/SS5YZ_P: U1501.6 (A); also elsewhere on the board
/SSerial 0-11/SS6AB_N: R1602.2, R1603.1, U1602.7 (B); also elsewhere on the board
/SSerial 0-11/SS6AB_P: R1601.2, R1602.1, U1602.6 (A); also elsewhere on the board
/SSerial 0-11/SS6YZ_N: U1601.7 (B); also elsewhere on the board
/SSerial 0-11/SS6YZ_P: U1601.6 (A); also elsewhere on the board
/SSerial 0-11/SS7AB_N: R1702.2, R1703.1, U1702.7 (B); also elsewhere on the board
/SSerial 0-11/SS7AB_P: R1701.2, R1702.1, U1702.6 (A); also elsewhere on the board
/SSerial 0-11/SS7YZ_N: U1701.7 (B); also elsewhere on the board
/SSerial 0-11/SS7YZ_P: U1701.6 (A); also elsewhere on the board
/SSerial 0-11/SS8AB_N: R1802.2, R1803.1, U1802.7 (B); also elsewhere on the board
/SSerial 0-11/SS8AB_P: R1801.2, R1802.1, U1802.6 (A); also elsewhere on the board
/SSerial 0-11/SS8YZ_N: U1801.7 (B); also elsewhere on the board
/SSerial 0-11/SS8YZ_P: U1801.6 (A); also elsewhere on the board
/SSerial 0-11/SS9AB_N: R1902.2, R1903.1, U1902.7 (B); also elsewhere on the board
/SSerial 0-11/SS9AB_P: R1901.2, R1902.1, U1902.6 (A); also elsewhere on the board
/SSerial 0-11/SS9YZ_N: U1901.7 (B); also elsewhere on the board
/SSerial 0-11/SS9YZ_P: U1901.6 (A); also elsewhere on the board
/SSerial 0-11/SS10AB_N: R2002.2, R2003.1, U2002.7 (B); also elsewhere on the board
/SSerial 0-11/SS10AB_P: R2001.2, R2002.1, U2002.6 (A); also elsewhere on the board
/SSerial 0-11/SS10YZ_N: U2001.7 (B); also elsewhere on the board
/SSerial 0-11/SS10YZ_P: U2001.6 (A); also elsewhere on the board
/SSerial 0-11/SS11AB_N: R2102.2, R2103.1, U2102.7 (B); also elsewhere on the board
/SSerial 0-11/SS11AB_P: R2101.2, R2102.1, U2102.6 (A); also elsewhere on the board
/SSerial 0-11/SS11YZ_N: U2101.7 (B); also elsewhere on the board
/SSerial 0-11/SS11YZ_P: U2101.6 (A); also elsewhere on the board
/SSerial 12-13/SS12AB_N: R2202.2, R2203.1, U2202.7 (B); also elsewhere on the board
/SSerial 12-13/SS12AB_P: R2201.2, R2202.1, U2202.6 (A); also elsewhere on the board
/SSerial 12-13/SS12YZ_N: U2201.7 (B); also elsewhere on the board
/SSerial 12-13/SS12YZ_P: U2201.6 (A); also elsewhere on the board
/SSerial 12-13/SS13AB_N: R2302.2, R2303.1, U2302.7 (B); also elsewhere on the board
/SSerial 12-13/SS13AB_P: R2301.2, R2302.1, U2302.6 (A); also elsewhere on the board
/SSerial 12-13/SS13YZ_N: U2301.7 (B); also elsewhere on the board
/SSerial 12-13/SS13YZ_P: U2301.6 (A); also elsewhere on the board
GND: C1101.2, C1102.2, C1201.2, C1202.2, C1301.2, C1302.2, C1401.2, C1402.2, C1501.2, C1502.2, C1601.2, C1602.2, C1701.2, C1702.2, C1801.2, C1802.2, C1901.2, C1902.2, C2001.2, C2002.2, C2101.2, C2102.2, C2201.2, C2202.2, C2301.2, C2302.2, R1103.2, R1203.2, R1303.2, R1403.2, R1503.2, R1603.2, R1703.2, R1803.2, R1903.2, R2003.2, R2103.2, R2203.2, R2303.2, U1101.5 (GND), U1102.2 (~RE), U1102.5 (GND), U1201.5 (GND), U1202.2 (~RE), U1202.5 (GND), U1301.5 (GND), U1302.2 (~RE), U1302.5 (GND), U1401.5 (GND), U1402.2 (~RE), U1402.5 (GND), U1501.5 (GND), U1502.2 (~RE), U1502.5 (GND), U1601.5 (GND), U1602.2 (~RE), U1602.5 (GND), U1701.5 (GND), U1702.2 (~RE), U1702.5 (GND), U1801.5 (GND), U1802.2 (~RE), U1802.5 (GND), U1901.5 (GND), U1902.2 (~RE), U1902.5 (GND), U2001.5 (GND), U2002.2 (~RE), U2002.5 (GND), U2101.5 (GND), U2102.2 (~RE), U2102.5 (GND), U2201.5 (GND), U2202.2 (~RE), U2202.5 (GND), U2301.5 (GND), U2302.2 (~RE), U2302.5 (GND); also elsewhere on the board

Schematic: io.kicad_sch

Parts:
C2401: 100n; C_0603_1608Metric
F4: 1A; Fuse_1206_3216Metric
J4: Parallel expansion port; IDC-Header_2x13_P2.54mm_Horizontal
JP41: IO Voltage; SolderJumper-3_P1.3mm_Bridged12_RoundedPad1.0x1.5mm
JP42: PULL-UP/DOWN; SolderJumper-3_P1.3mm_Bridged12_RoundedPad1.0x1.5mm
JP43: Breakout Power; SolderJumper-3_P1.3mm_Bridged12_RoundedPad1.0x1.5mm
Q2401: SS8550; SOT-23
R2401, R2402: 1k; R_0603_1608Metric
R2403: 4k99; R_0603_1608Metric
R2404: 4k7; R_0603_1608Metric
RN2401, RN2402, RN2403, RN2404: 4k7; R_Array_Convex_4x0603
U2401: 74CB3T16210DGG; TSSOP-48_6.1x12.5mm_P0.5mm

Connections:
+3V3: JP41.3 (B); also elsewhere on the board
+5V: JP41.1 (A), Q2401.2 (E), R2402.1; also elsewhere on the board
+5VP: F4.1; also elsewhere on the board
/FPGA Bank 0 1/Parallel expansion port/FPGA_IO0: U2401.5 (1A4); also elsewhere on the board
/FPGA Bank 0 1/Parallel expansion port/FPGA_IO1: U2401.6 (1A5); also elsewhere on the board
/FPGA Bank 0 1/Parallel expansion port/FPGA_IO2: U2401.7 (1A6); also elsewhere on the board
/FPGA Bank 0 1/Parallel expansion port/FPGA_IO3: U2401.9 (1A7); also elsewhere on the board
/FPGA Bank 0 1/Parallel expansion port/FPGA_IO4: U2401.10 (1A8); also elsewhere on the board
/FPGA Bank 0 1/Parallel expansion port/FPGA_IO5: U2401.11 (1A9); also elsewhere on the board
/FPGA Bank 0 1/Parallel expansion port/FPGA_IO6: U2401.12 (1A10); also elsewhere on the board
/FPGA Bank 0 1/Parallel expansion port/FPGA_IO7: U2401.13 (2A1); also elsewhere on the board
/FPGA Bank 0 1/Parallel expansion port/FPGA_IO8: U2401.14 (2A2); also elsewhere on the board
/FPGA Bank 0 1/Parallel expansion port/FPGA_IO9: U2401.16 (2A3); also elsewhere on the board
/FPGA Bank 0 1/Parallel expansion port/FPGA_IO10: U2401.18 (2A4); also elsewhere on the board
/FPGA Bank 0 1/Parallel expansion port/FPGA_IO11: U2401.19 (2A5); also elsewhere on the board
/FPGA Bank 0 1/Parallel expansion port/FPGA_IO12: U2401.20 (2A6); also elsewhere on the board
/FPGA Bank 0 1/Parallel expansion port/FPGA_IO13: U2401.21 (2A7); also elsewhere on the board
/FPGA Bank 0 1/Parallel expansion port/FPGA_IO14: U2401.22 (2A8); also elsewhere on the board
/FPGA Bank 0 1/Parallel expansion port/FPGA_IO15: U2401.23 (2A9); also elsewhere on the board
/FPGA Bank 0 1/Parallel expansion port/FPGA_IO16: U2401.24 (2A10); also elsewhere on the board
/FPGA Bank 0 1/Parallel expansion port/IO0: J4.1, RN2401.4 (R4.1), U2401.43 (1B4)
/FPGA Bank 0 1/Parallel expansion port/IO1: J4.2, RN2401.3 (R3.1), U2401.42 (1B5)
/FPGA Bank 0 1/Parallel expansion port/IO2: J4.3, RN2401.2 (R2.1), U2401.40 (1B6)
/FPGA Bank 0 1/Parallel expansion port/IO3: J4.4, RN2401.1 (R1.1), U2401.39 (1B7)
/FPGA Bank 0 1/Parallel expansion port/IO4: J4.5, RN2402.4 (R4.1), U2401.38 (1B8)
/FPGA Bank 0 1/Parallel expansion port/IO5: J4.6, RN2402.3 (R3.1), U2401.37 (1B9)
/FPGA Bank 0 1/Parallel expansion port/IO6: J4.7, RN2402.2 (R2.1), U2401.36 (1B10)
/FPGA Bank 0 1/Parallel expansion port/IO7: J4.8, RN2402.1 (R1.1), U2401.35 (2B1)
/FPGA Bank 0 1/Parallel expansion port/IO8: J4.9, RN2403.1 (R1.1), U2401.34 (2B2)
/FPGA Bank 0 1/Parallel expansion port/IO9: J4.11, RN2403.2 (R2.1), U2401.33 (2B3)
/FPGA Bank 0 1/Parallel expansion port/IO10: J4.13, RN2403.3 (R3.1), U2401.31 (2B4)
/FPGA Bank 0 1/Parallel expansion port/IO11: J4.15, RN2403.4 (R4.1), U2401.30 (2B5)
/FPGA Bank 0 1/Parallel expansion port/IO12: J4.17, RN2404.1 (R1.1), U2401.29 (2B6)
/FPGA Bank 0 1/Parallel expansion port/IO13: J4.19, RN2404.2 (R2.1), U2401.28 (2B7)
/FPGA Bank 0 1/Parallel expansion port/IO14: J4.21, RN2404.3 (R3.1), U2401.27 (2B8)
/FPGA Bank 0 1/Parallel expansion port/IO15: J4.23, RN2404.4 (R4.1), U2401.26 (2B9)
/FPGA Bank 0 1/Parallel expansion port/IO16: J4.25, R2404.2, U2401.25 (2B10)
GND: C2401.2, J4.10, J4.12, J4.14, J4.16, JP42.3 (B), JP43.3 (B), R2403.2, U2401.8 (GND), U2401.17 (GND), U2401.32 (GND), U2401.41 (GND), U2401.47 (2~OE), U2401.48 (1~OE); also elsewhere on the board
unnamed: J4.18, J4.20, J4.22, J4.24, J4.26, JP43.2 (C)
unnamed: JP41.2 (C), JP42.1 (A), R2401.1
unnamed: JP42.2 (C), R2404.1, RN2401.5 (R4.2), RN2401.6 (R3.2), RN2401.7 (R2.2), RN2401.8 (R1.2), RN2402.5 (R4.2), RN2402.6 (R3.2), RN2402.7 (R2.2), RN2402.8 (R1.2), RN2403.5 (R4.2), RN2403.6 (R3.2), RN2403.7 (R2.2), RN2403.8 (R1.2), RN2404.5 (R4.2), RN2404.6 (R3.2), RN2404.7 (R2.2), RN2404.8 (R1.2)
unnamed: F4.2, JP43.1 (A)
unnamed: Q2401.1 (B), R2401.2
unnamed: C2401.1, Q2401.3 (C), R2402.2, R2403.1, U2401.15 (VCC)

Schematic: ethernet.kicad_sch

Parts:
C601, C603, C610, C611: 4.7uF; C_0603_1608Metric
C602, C604, C605, C606, C607, C608, C609, C612, C613, C614, C615: 100n; C_0603_1608Metric
J5: Ethernet; RJ45_Hanrun_HR911105A_Horizontal
L601, L602, L603: 100R@100MHz; L_0805_2012Metric
R601: 1k; R_0603_1608Metric
R602, R611: 10k; R_0603_1608Metric
R603: 3k01 1%; R_0603_1608Metric
R604, R605, R610: 300R; R_0603_1608Metric
R606, R607, R608, R609: 49R9 1%; R_0603_1608Metric
RN601, RN602: 1k; R_Array_Convex_4x0603
U601: KSZ8851-16MLL; LQFP-48_7x7mm_P0.5mm
U602: 93LC46B/SN; SOIC-8_3.9x4.9mm_P1.27mm

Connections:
+3V3: C601.1, C602.1, C604.1, C606.1, C613.1, J5.9, J5.12, L601.1, R601.1, R611.1, U601.27 (VDD_IO), U601.38 (VDD_IO), U601.46 (VDD_IO), U602.6 (ORG), U602.8 (VCC); also elsewhere on the board
/FPGA Bank 0 1/Ethernet/CLOCK: U601.24 (X1); also elsewhere on the board
/FPGA Bank 0 1/Ethernet/CMD: U601.11 (CMD); also elsewhere on the board
/FPGA Bank 0 1/Ethernet/CS: U601.15 (EECS), U602.1 (CS)
/FPGA Bank 0 1/Ethernet/DIO: R610.1, R611.2, U601.9 (EDD_IO), U602.3 (DI)
/FPGA Bank 0 1/Ethernet/SCLK: U601.10 (EESK), U602.2 (SCLK)
/FPGA Bank 0 1/Ethernet/SD0: U601.48 (SD0); also elsewhere on the board
/FPGA Bank 0 1/Ethernet/SD1: U601.47 (SD1); also elsewhere on the board
/FPGA Bank 0 1/Ethernet/SD2: U601.45 (SD2); also elsewhere on the board
/FPGA Bank 0 1/Ethernet/SD3: U601.44 (SD3); also elsewhere on the board
/FPGA Bank 0 1/Ethernet/SD4: U601.43 (SD4); also elsewhere on the board
/FPGA Bank 0 1/Ethernet/SD5: U601.42 (SD5); also elsewhere on the board
/FPGA Bank 0 1/Ethernet/SD6: U601.41 (SD6); also elsewhere on the board
/FPGA Bank 0 1/Ethernet/SD7: U601.40 (SD7); also elsewhere on the board
/FPGA Bank 0 1/Ethernet/SD8: RN602.6 (R3.2), U601.39 (SD8); also elsewhere on the board
/FPGA Bank 0 1/Ethernet/SD9: RN601.8 (R1.2), U601.36 (SD9); also elsewhere on the board
/FPGA Bank 0 1/Ethernet/SD10: RN602.5 (R4.2), U601.35 (SD10); also elsewhere on the board
/FPGA Bank 0 1/Ethernet/SD11: RN601.5 (R4.2), U601.34 (SD11); also elsewhere on the board
/FPGA Bank 0 1/Ethernet/SD12: RN602.7 (R2.2), U601.33 (SD12); also elsewhere on the board
/FPGA Bank 0 1/Ethernet/SD13: RN601.6 (R3.2), U601.32 (SD13); also elsewhere on the board
/FPGA Bank 0 1/Ethernet/SD14: RN602.8 (R1.2), U601.31 (SD14); also elsewhere on the board
/FPGA Bank 0 1/Ethernet/SD15: RN601.7 (R2.2), U601.30 (SD15); also elsewhere on the board
/FPGA Bank 0 1/Ethernet/~CS: U601.12 (~CS); also elsewhere on the board
/FPGA Bank 0 1/Ethernet/~INTR: R601.2, U601.4 (~INTR); also elsewhere on the board
/FPGA Bank 0 1/Ethernet/~RD: U601.5 (~RD); also elsewhere on the board
/FPGA Bank 0 1/Ethernet/~RST: R602.1, U601.23 (~RST); also elsewhere on the board
/FPGA Bank 0 1/Ethernet/~WR: U601.6 (~WR); also elsewhere on the board
GND: C601.2, C602.2, C603.2, C604.2, C605.2, C606.2, C607.2, C608.2, C609.2, C610.2, C611.2, C612.2, C613.2, C614.2, C615.2, L603.2, R602.2, R603.2, RN601.1 (R1.1), RN601.2 (R2.1), RN601.3 (R3.1), RN601.4 (R4.1), RN602.1 (R1.1), RN602.2 (R2.1), RN602.3 (R3.1), RN602.4 (R4.1), U601.7 (DGND), U601.13 (AGND), U601.18 (AGND), U601.26 (DGND), U601.28 (DGND), U601.37 (DGND), U602.5 (GND); also elsewhere on the board
GNDS: J5.8, J5.SH, L603.1
unnamed: C612.1, R606.2, R607.2
unnamed: C614.1, R608.2, R609.2
unnamed: J5.10, R604.2
unnamed: J5.11, R605.2
unnamed: C603.1, C605.1, C615.1, J5.4 (TCT), J5.5 (RCT), L601.2, U601.21 (VDD_A3.3)
unnamed: J5.3 (RD+), R608.1, U601.16 (RXP1)
unnamed: J5.6 (RD-), R609.1, U601.17 (PXM1)
unnamed: J5.1 (TD+), R606.1, U601.19 (TXP1)
unnamed: J5.2 (TD-), R607.1, U601.20 (TXM1)
unnamed: R603.1, U601.22 (ISET)
unnamed: R604.1, U601.2 (P1LED0)
unnamed: R605.1, U601.1 (P1LED1)
unnamed: C609.1, C611.1, L602.1, U601.14 (VDD_A1.8)
unnamed: C607.1, C608.1, C610.1, L602.2, U601.8 (VDD_CO1.8), U601.29 (VDD_D1.8)
unnamed: R610.2, U602.4 (DO)

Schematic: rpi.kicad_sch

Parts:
C701, C702, C703: 100n; C_0603_1608Metric
JP2: HAT EEPROM WP; SolderJumper-2_P1.3mm_Open_RoundedPad1.0x1.5mm
R701, R702: 3k9; R_0603_1608Metric
R703: 1k; R_0603_1608Metric
U2: RaspberryPi-4/5; Raspberry_Pi_5_Socketed_THT_FaceDown_MountingHoles
U701: 24LC32AT-x/OT; SOT-23-5

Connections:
+3V3: C703.1, R701.1, R702.1, R703.1, U701.4 (VCC); also elsewhere on the board
+5V: U2.2 (5V), U2.4 (5V); also elsewhere on the board
/FPGA Bank 2 3/Raspberry Pi/RX: U2.10 (GPIO15/RXD); also elsewhere on the board
/FPGA Bank 2 3/Raspberry Pi/SCL: U2.5 (SCL/GPIO3); also elsewhere on the board
/FPGA Bank 2 3/Raspberry Pi/SCLK: U2.23 (SCLK0/GPIO11); also elsewhere on the board
/FPGA Bank 2 3/Raspberry Pi/SDA: U2.3 (SDA/GPIO2); also elsewhere on the board
/FPGA Bank 2 3/Raspberry Pi/SPICS: U2.24 (~CE0/GPIO8); also elsewhere on the board
/FPGA Bank 2 3/Raspberry Pi/SPIIN: U2.21 (MISO0/GPIO9); also elsewhere on the board
/FPGA Bank 2 3/Raspberry Pi/SPIOUT: U2.19 (MOSI0/GPIO10); also elsewhere on the board
/FPGA Bank 2 3/Raspberry Pi/TX: U2.8 (GPIO14/TXD); also elsewhere on the board
GND: C701.2, C702.2, C703.2, JP2.1 (A), U2.6 (GND), U2.9 (GND), U2.14 (GND), U2.20 (GND), U2.25 (GND), U2.30 (GND), U2.34 (GND), U2.39 (GND), U701.2 (GND); also elsewhere on the board
unnamed: C701.1, U2.17 (3V3)
unnamed: C702.1, U2.1 (3V3)
unnamed: JP2.2 (B), R703.2, U701.5 (WP)
unnamed: R702.2, U2.28 (ID_SC/GPIO1), U701.1 (SCL)
unnamed: R701.2, U2.27 (ID_SD/GPIO0), U701.3 (SDA)

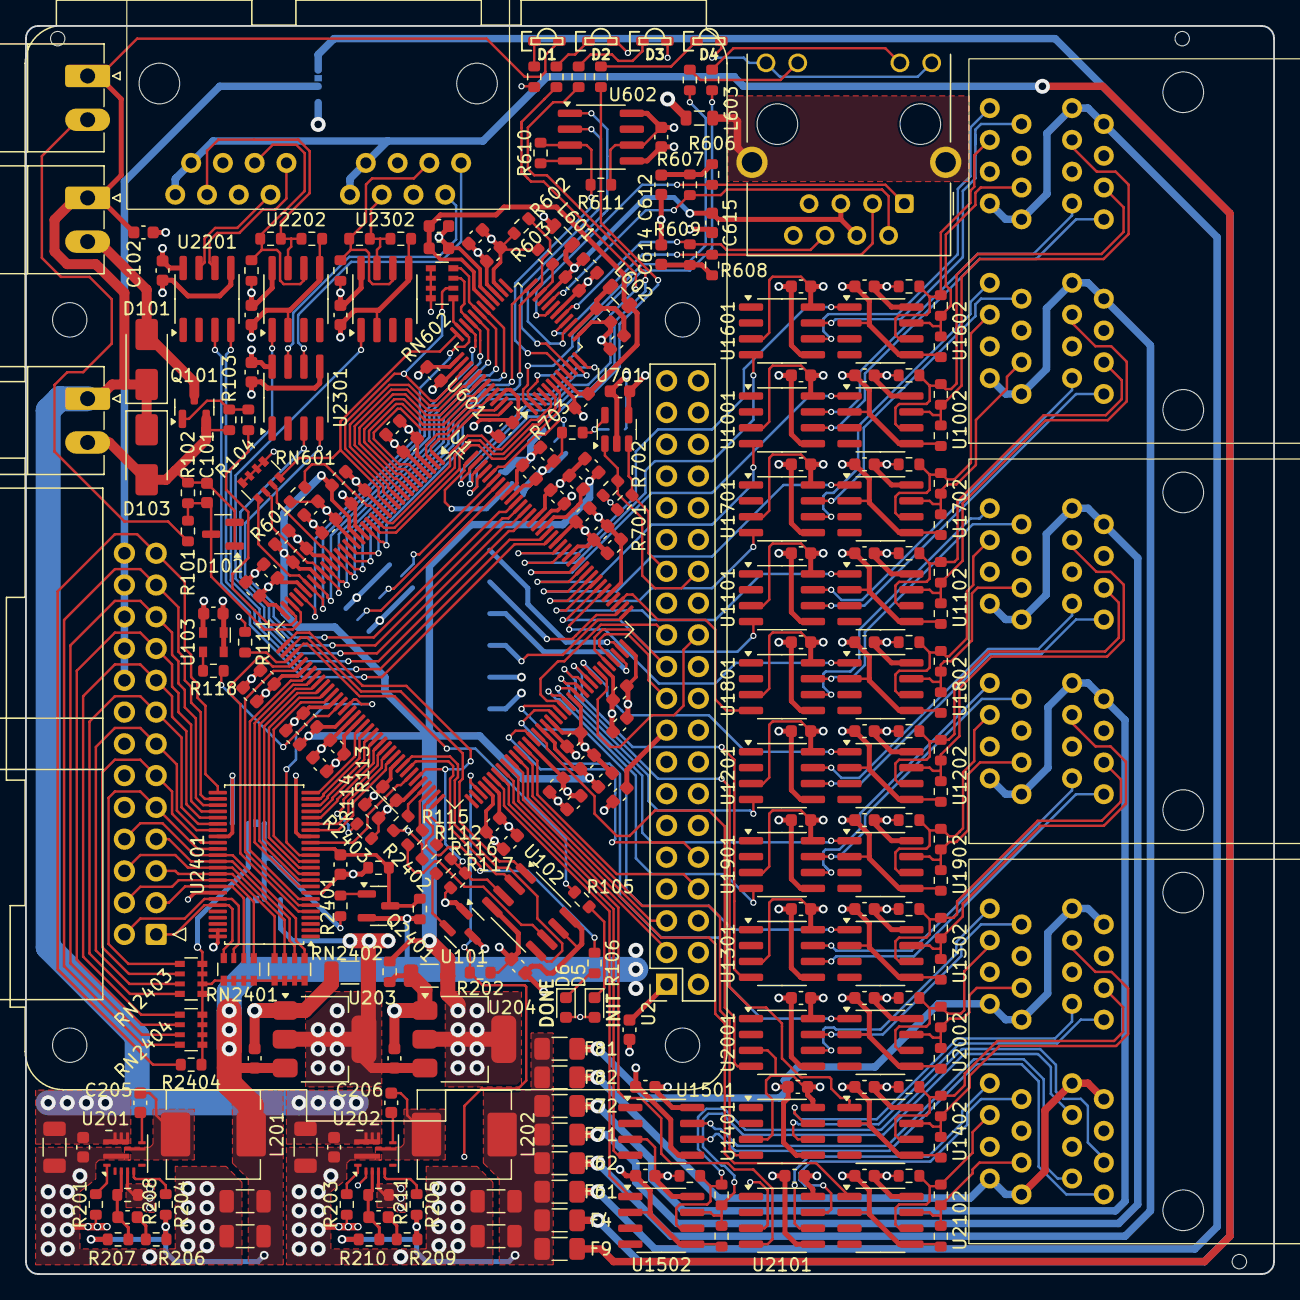
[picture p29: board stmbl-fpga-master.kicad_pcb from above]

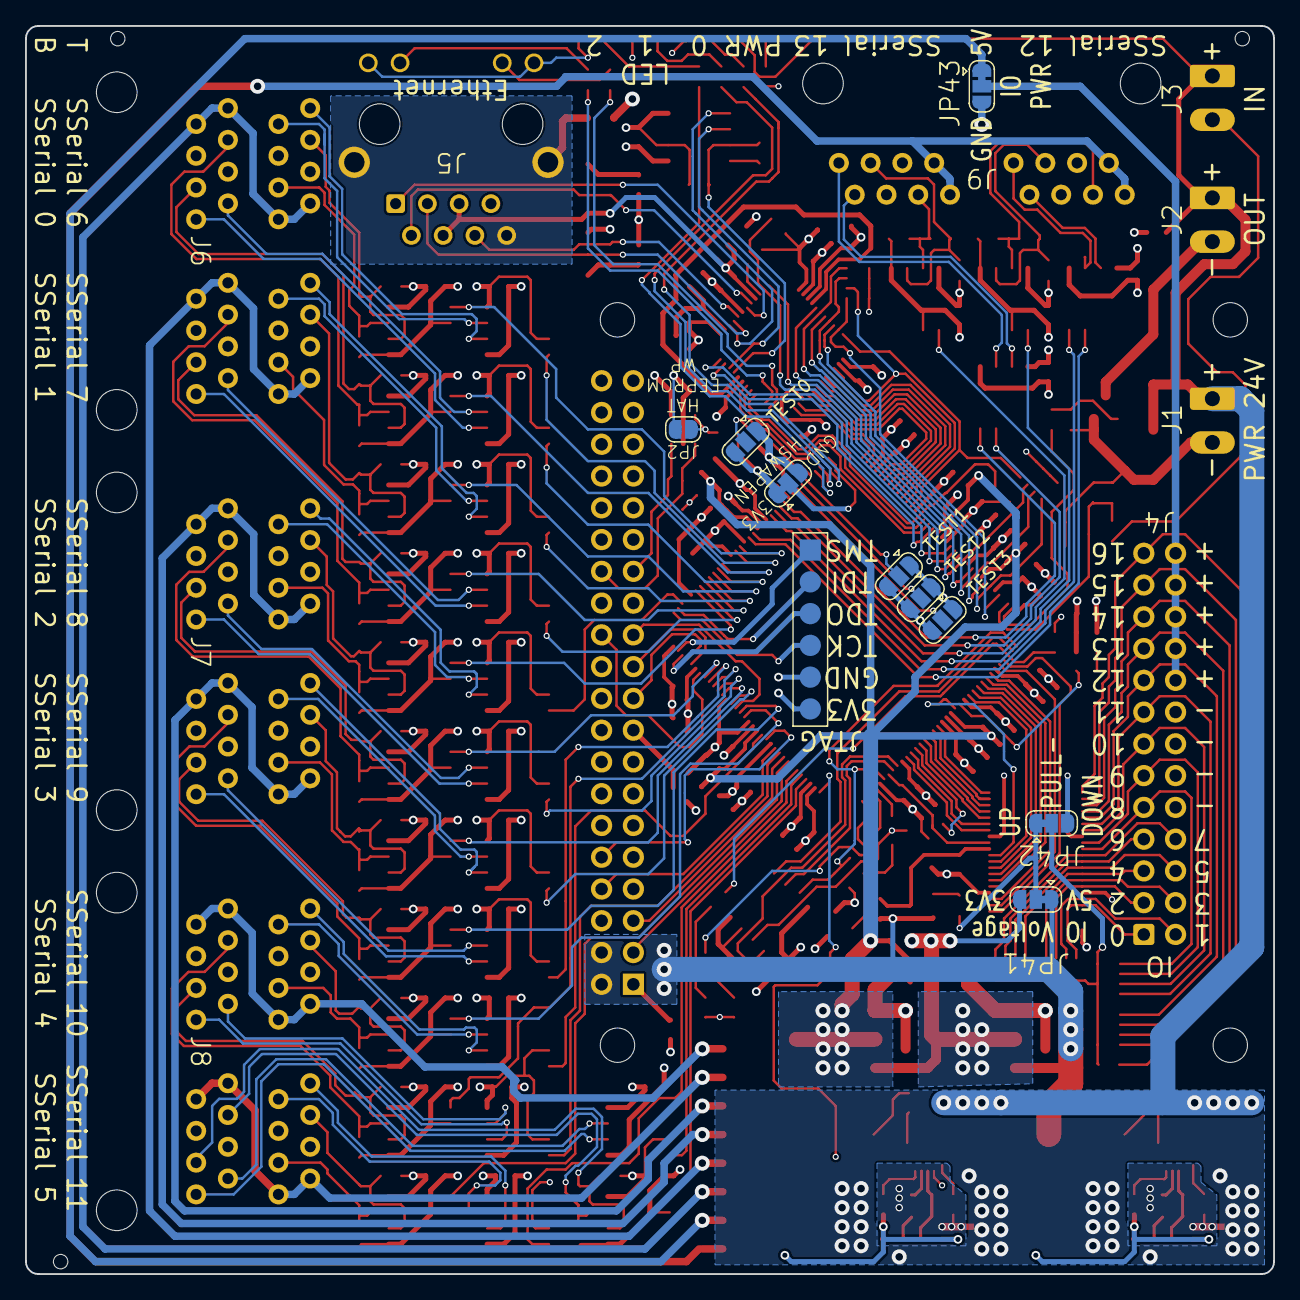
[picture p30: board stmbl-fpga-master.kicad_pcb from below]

Board: 4 copper layers, 99.8 x 99.8 mm, 284 parts (10 on the bottom side), 246 nets.

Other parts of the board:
TEST0, TEST1, TEST2, TEST3: SolderJumper-3_P1.3mm_Open_RoundedPad1.0x1.5mm

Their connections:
+3V3: TEST0.3 (B), TEST1.3 (B), TEST2.3 (B), TEST3.3 (B); also elsewhere on the board
/FPGA Bank 2 3/TEST0: TEST0.2 (C); also elsewhere on the board
/FPGA Bank 2 3/TEST1: TEST1.2 (C); also elsewhere on the board
/FPGA Bank 2 3/TEST2: TEST2.2 (C); also elsewhere on the board
/FPGA Bank 2 3/TEST3: TEST3.2 (C); also elsewhere on the board
GND: TEST0.1 (A), TEST1.1 (A), TEST2.1 (A), TEST3.1 (A); also elsewhere on the board

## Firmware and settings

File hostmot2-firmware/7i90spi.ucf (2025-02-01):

NET "CLK" TNM_NET = "CLK";
TIMESPEC "TS_CLK" = PERIOD "CLK" 19.9 ns HIGH 50 %;

NET "COM_SPICLK" TNM_NET = "COM_SPICLK";
TIMESPEC "TS_COM_SPICLK" = PERIOD "COM_SPICLK" 9 ns HIGH 50 %;

OFFSET = OUT 12 ns AFTER "COM_SPICLK"  ;
OFFSET = IN 8 ns BEFORE "COM_SPICLK"  ;

NET	"COM_SPICLK"	LOC ="P55"	 | IOSTANDARD = LVTTL;
NET	"COM_SPIIN"	LOC ="P56"	 | IOSTANDARD = LVTTL;
NET	"COM_SPIOUT"	LOC ="P57"	 | IOSTANDARD = LVTTL | DRIVE = 4 | SLEW = FAST ;
NET	"COM_SPICS"	LOC ="P58"	 | IOSTANDARD = LVTTL;

NET	"TEST0"	LOC ="P59"	 | IOSTANDARD = LVTTL;

NET	"RECONFIG"	LOC ="P67"	 | IOSTANDARD = LVTTL | DRIVE = 4 | SLEW = SLOW ;
NET	"SPICS"		LOC ="P38"	 | IOSTANDARD = LVTTL | DRIVE = 4 | SLEW = SLOW ;
NET	"SPIIN"		LOC ="P65"	 | IOSTANDARD = LVTTL;
NET	"SPIOUT"	LOC ="P64"	 | IOSTANDARD = LVTTL | DRIVE = 4 | SLEW = SLOW ;
NET	"SPICLK"	LOC ="P70"	 | IOSTANDARD = LVTTL | DRIVE = 4 | SLEW = SLOW ;
NET	"NINIT"		LOC ="P39"	| IOSTANDARD = LVTTL | DRIVE = 12 | SLEW = SLOW ; 
NET	"CLK"		LOC ="P50"	 | IOSTANDARD = LVTTL | DRIVE = 4 | SLEW = SLOW ;
NET	"LEDS<1>"	LOC ="P74"	 | IOSTANDARD = LVTTL | DRIVE = 8 | SLEW = SLOW ;
NET	"LEDS<0>"	LOC ="P75"	 | IOSTANDARD = LVTTL | DRIVE = 8 | SLEW = SLOW ;
NET	"IOBITS<0>"	LOC ="P35"	 | IOSTANDARD = LVTTL | DRIVE = 24 | SLEW = SLOW ;
NET	"IOBITS<1>"	LOC ="P34"	 | IOSTANDARD = LVTTL | DRIVE = 24 | SLEW = SLOW ;
NET	"IOBITS<24>"	LOC ="P33"	 | IOSTANDARD = LVTTL | DRIVE = 24 | SLEW = SLOW ;
NET	"IOBITS<25>"	LOC ="P32"	 | IOSTANDARD = LVTTL | DRIVE = 24 | SLEW = SLOW ;
NET	"IOBITS<48>"	LOC ="P30"	 | IOSTANDARD = LVTTL | DRIVE = 24 | SLEW = SLOW ;
NET	"IOBITS<49>"	LOC ="P29"	 | IOSTANDARD = LVTTL | DRIVE = 24 | SLEW = SLOW ;
NET	"IOBITS<2>"	LOC ="P27"	 | IOSTANDARD = LVTTL | DRIVE = 24 | SLEW = SLOW ;
NET	"IOBITS<3>"	LOC ="P26"	 | IOSTANDARD = LVTTL | DRIVE = 24 | SLEW = SLOW ;
NET	"IOBITS<26>"	LOC ="P24"	 | IOSTANDARD = LVTTL | DRIVE = 24 | SLEW = SLOW ;
NET	"IOBITS<27>"	LOC ="P23"	 | IOSTANDARD = LVTTL | DRIVE = 24 | SLEW = SLOW ;
NET	"IOBITS<50>"	LOC ="P22"	 | IOSTANDARD = LVTTL | DRIVE = 24 | SLEW = SLOW ;
NET	"IOBITS<51>"	LOC ="P21"	 | IOSTANDARD = LVTTL | DRIVE = 24 | SLEW = SLOW ;
NET	"IOBITS<4>"	LOC ="P17"	 | IOSTANDARD = LVTTL | DRIVE = 24 | SLEW = SLOW ;
NET	"IOBITS<5>"	LOC ="P16"	 | IOSTANDARD = LVTTL | DRIVE = 24 | SLEW = SLOW ;
NET	"IOBITS<28>"	LOC ="P15"	 | IOSTANDARD = LVTTL | DRIVE = 24 | SLEW = SLOW ;
NET	"IOBITS<29>"	LOC ="P14"	 | IOSTANDARD = LVTTL | DRIVE = 24 | SLEW = SLOW ;
NET	"IOBITS<52>"	LOC ="P12"	 | IOSTANDARD = LVTTL | DRIVE = 24 | SLEW = SLOW ;
NET	"IOBITS<53>"	LOC ="P11"	 | IOSTANDARD = LVTTL | DRIVE = 24 | SLEW = SLOW ;
NET	"IOBITS<6>"	LOC ="P10"	 | IOSTANDARD = LVTTL | DRIVE = 24 | SLEW = SLOW ;
NET	"IOBITS<7>"	LOC ="P9"	 | IOSTANDARD = LVTTL | DRIVE = 24 | SLEW = SLOW ;
NET	"IOBITS<30>"	LOC ="P8"	 | IOSTANDARD = LVTTL | DRIVE = 24 | SLEW = SLOW ;
NET	"IOBITS<31>"	LOC ="P7"	 | IOSTANDARD = LVTTL | DRIVE = 24 | SLEW = SLOW ;
NET	"IOBITS<54>"	LOC ="P6"	 | IOSTANDARD = LVTTL | DRIVE = 24 | SLEW = SLOW ;
NET	"IOBITS<55>"	LOC ="P5"	 | IOSTANDARD = LVTTL | DRIVE = 24 | SLEW = SLOW ;
NET	"IOBITS<8>"	LOC ="P2"	 | IOSTANDARD = LVTTL | DRIVE = 24 | SLEW = SLOW ;
NET	"IOBITS<9>"	LOC ="P1"	 | IOSTANDARD = LVTTL | DRIVE = 24 | SLEW = SLOW ;
NET	"IOBITS<32>"	LOC ="P142"	 | IOSTANDARD = LVTTL | DRIVE = 24 | SLEW = SLOW ;
NET	"IOBITS<33>"	LOC ="P141"	 | IOSTANDARD = LVTTL | DRIVE = 24 | SLEW = SLOW ;
NET	"IOBITS<56>"	LOC ="P140"	 | IOSTANDARD = LVTTL | DRIVE = 24 | SLEW = SLOW ;
NET	"IOBITS<57>"	LOC ="P139"	 | IOSTANDARD = LVTTL | DRIVE = 24 | SLEW = SLOW ;
NET	"IOBITS<10>"	LOC ="P138"	 | IOSTANDARD = LVTTL | DRIVE = 24 | SLEW = SLOW ;
NET	"IOBITS<11>"	LOC ="P137"	 | IOSTANDARD = LVTTL | DRIVE = 24 | SLEW = SLOW ;
NET	"IOBITS<34>"	LOC ="P134"	 | IOSTANDARD = LVTTL | DRIVE = 24 | SLEW = SLOW ;
NET	"IOBITS<35>"	LOC ="P133"	 | IOSTANDARD = LVTTL | DRIVE = 24 | SLEW = SLOW ;
NET	"IOBITS<58>"	LOC ="P132"	 | IOSTANDARD = LVTTL | DRIVE = 24 | SLEW = SLOW ;
NET	"IOBITS<59>"	LOC ="P131"	 | IOSTANDARD = LVTTL | DRIVE = 24 | SLEW = SLOW ;
NET	"IOBITS<12>"	LOC ="P127"	 | IOSTANDARD = LVTTL | DRIVE = 24 | SLEW = SLOW ;
NET	"IOBITS<13>"	LOC ="P126"	 | IOSTANDARD = LVTTL | DRIVE = 24 | SLEW = SLOW ;
NET	"IOBITS<36>"	LOC ="P124"	 | IOSTANDARD = LVTTL | DRIVE = 24 | SLEW = SLOW ;
NET	"IOBITS<37>"	LOC ="P123"	 | IOSTANDARD = LVTTL | DRIVE = 24 | SLEW = SLOW ;
NET	"IOBITS<60>"	LOC ="P121"	 | IOSTANDARD = LVTTL | DRIVE = 24 | SLEW = SLOW ;
NET	"IOBITS<61>"	LOC ="P120"	 | IOSTANDARD = LVTTL | DRIVE = 24 | SLEW = SLOW ;
NET	"IOBITS<14>"	LOC ="P119"	 | IOSTANDARD = LVTTL | DRIVE = 24 | SLEW = SLOW ;
NET	"IOBITS<15>"	LOC ="P118"	 | IOSTANDARD = LVTTL | DRIVE = 24 | SLEW = SLOW ;
NET	"IOBITS<38>"	LOC ="P117"	 | IOSTANDARD = LVTTL | DRIVE = 24 | SLEW = SLOW ;
NET	"IOBITS<39>"	LOC ="P116"	 | IOSTANDARD = LVTTL | DRIVE = 24 | SLEW = SLOW ;
NET	"IOBITS<62>"	LOC ="P115"	 | IOSTANDARD = LVTTL | DRIVE = 24 | SLEW = SLOW ;
NET	"IOBITS<63>"	LOC ="P114"	 | IOSTANDARD = LVTTL | DRIVE = 24 | SLEW = SLOW ;
NET	"IOBITS<16>"	LOC ="P112"	 | IOSTANDARD = LVTTL | DRIVE = 24 | SLEW = SLOW ;
NET	"IOBITS<17>"	LOC ="P111"	 | IOSTANDARD = LVTTL | DRIVE = 24 | SLEW = SLOW ;
NET	"IOBITS<40>"	LOC ="P105"	 | IOSTANDARD = LVTTL | DRIVE = 24 | SLEW = SLOW ;
NET	"IOBITS<41>"	LOC ="P104"	 | IOSTANDARD = LVTTL | DRIVE = 24 | SLEW = SLOW ;
NET	"IOBITS<64>"	LOC ="P102"	 | IOSTANDARD = LVTTL | DRIVE = 24 | SLEW = SLOW ;
NET	"IOBITS<65>"	LOC ="P101"	 | IOSTANDARD = LVTTL | DRIVE = 24 | SLEW = SLOW ;
NET	"IOBITS<18>"	LOC ="P100"	 | IOSTANDARD = LVTTL | DRIVE = 24 | SLEW = SLOW ;
NET	"IOBITS<19>"	LOC ="P99"	 | IOSTANDARD = LVTTL | DRIVE = 24 | SLEW = SLOW ;
NET	"IOBITS<42>"	LOC ="P98"	 | IOSTANDARD = LVTTL | DRIVE = 24 | SLEW = SLOW ;
NET	"IOBITS<43>"	LOC ="P97"	 | IOSTANDARD = LVTTL | DRIVE = 24 | SLEW = SLOW ;
NET	"IOBITS<66>"	LOC ="P95"	 | IOSTANDARD = LVTTL | DRIVE = 24 | SLEW = SLOW ;
NET	"IOBITS<67>"	LOC ="P94"	 | IOSTANDARD = LVTTL | DRIVE = 24 | SLEW = SLOW ;
NET	"IOBITS<20>"	LOC ="P93"	 | IOSTANDARD = LVTTL | DRIVE = 24 | SLEW = SLOW ;
NET	"IOBITS<21>"	LOC ="P92"	 | IOSTANDARD = LVTTL | DRIVE = 24 | SLEW = SLOW ;
NET	"IOBITS<44>"	LOC ="P88"	 | IOSTANDARD = LVTTL | DRIVE = 24 | SLEW = SLOW ;
NET	"IOBITS<45>"	LOC ="P87"	 | IOSTANDARD = LVTTL | DRIVE = 24 | SLEW = SLOW ;
NET	"IOBITS<68>"	LOC ="P85"	 | IOSTANDARD = LVTTL | DRIVE = 24 | SLEW = SLOW ;
NET	"IOBITS<69>"	LOC ="P84"	 | IOSTANDARD = LVTTL | DRIVE = 24 | SLEW = SLOW ;
NET	"IOBITS<22>"	LOC ="P83"	 | IOSTANDARD = LVTTL | DRIVE = 24 | SLEW = SLOW ;
NET	"IOBITS<23>"	LOC ="P82"	 | IOSTANDARD = LVTTL | DRIVE = 24 | SLEW = SLOW ;
NET	"IOBITS<46>"	LOC ="P81"	 | IOSTANDARD = LVTTL | DRIVE = 24 | SLEW = SLOW ;
NET	"IOBITS<47>"	LOC ="P80"	 | IOSTANDARD = LVTTL | DRIVE = 24 | SLEW = SLOW ;
NET	"IOBITS<70>"	LOC ="P79"	 | IOSTANDARD = LVTTL | DRIVE = 24 | SLEW = SLOW ;
NET	"IOBITS<71>"	LOC ="P78"	 | IOSTANDARD = LVTTL | DRIVE = 24 | SLEW = SLOW ;
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

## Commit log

2025-02-16 fixed some stuff
    [ethernet.kicad_sch, fpga_misc.kicad_sch, rpi.kicad_sch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]
2025-03-09 some changes in schematic and added pcb
    [ethernet.kicad_sch, fpga_misc.kicad_sch, stmbl-fpga-master.kicad_pcb]
2025-03-09 jlcpcb production files
    [BOM-stmbl-fpga-master.csv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]
2025-03-16 updated 3d models
    [HC-RJ45-5622-2-6-Körper.step, HC-RJ45-5622-2-6-KörperPad.step, HC-RJ45-5622-2-6.FCStd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]
2025-07-15 updated wrong traces on kicad_pcb
    [BOM-stmbl-fpga-master.csv, ethernet.kicad_sch, fpga_bank_0_1.kicad_sch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]
2025-07-20 Added 3D case step and source
    [stmblv5_ss-kitcase.step]
